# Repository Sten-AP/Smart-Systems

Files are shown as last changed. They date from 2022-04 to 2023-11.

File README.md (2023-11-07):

# Smart Systems

Sten Hulsbergen<br/>
2ITIOT<br/>

# Portfolio

## Korte beschrijving van het project

Het project is het ontwerpen van een smart car. De PCB's worden individueel gemaakt en de auto moet automatisch alsook manueel bestuurbaar kunnen zijn met embedded software.

### Wat is het doel van het project?

Het doel is om een analyse te maken en met deze analyse het project op te bouwen. Dit houdt in dat er PCB's ontworpen moesten worden, gemaakt en bestukt. Later dan software ontwikkelen en de wagen testen.

### Wat is er gerealiseerd?

- Analyse gemaakt
- PCB’s ontwropen
- PCB’s gefreesd
- PCB’s bestukt
- Software geschreven
- Wagen getest

## Toelichten van het finale ontwerp van het project:
### Wat waren de vereisten van het project?

De auto moest twee UART connectoren bevatten, drie I2C connectoren, de regelaar 7805 vervangen door een LDL1117 van 3.3V en 5V, polariteitsbeveiliging voorzien, motordriver aanpassen naar een SMD-type en een OLED-scherm met I2C sturing. Naast de sturing moesten een aantal sensoren voorzien worden, een linetracker, IR- en ultrasone afstandssensoren. Ook zullen er verkeerssignalisaties ontwikkeld moeten worden zoals verkeerslichten, slagbomen,... Als laatste moet de wagen manueel alsook automatisch bestuurd kunnen worden en een patroon kunnen rijden.

### Effectieve ontwerpen:
#### PCB Design
##### Sturingschakeling

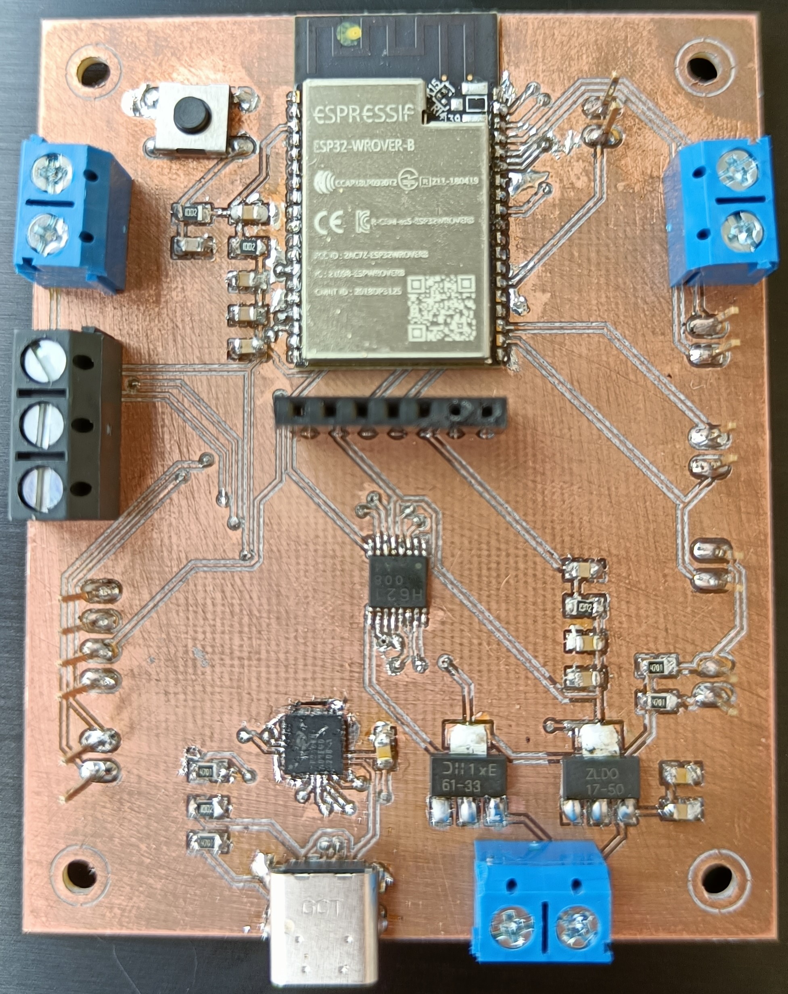
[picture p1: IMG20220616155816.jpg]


##### Sensorschakeling

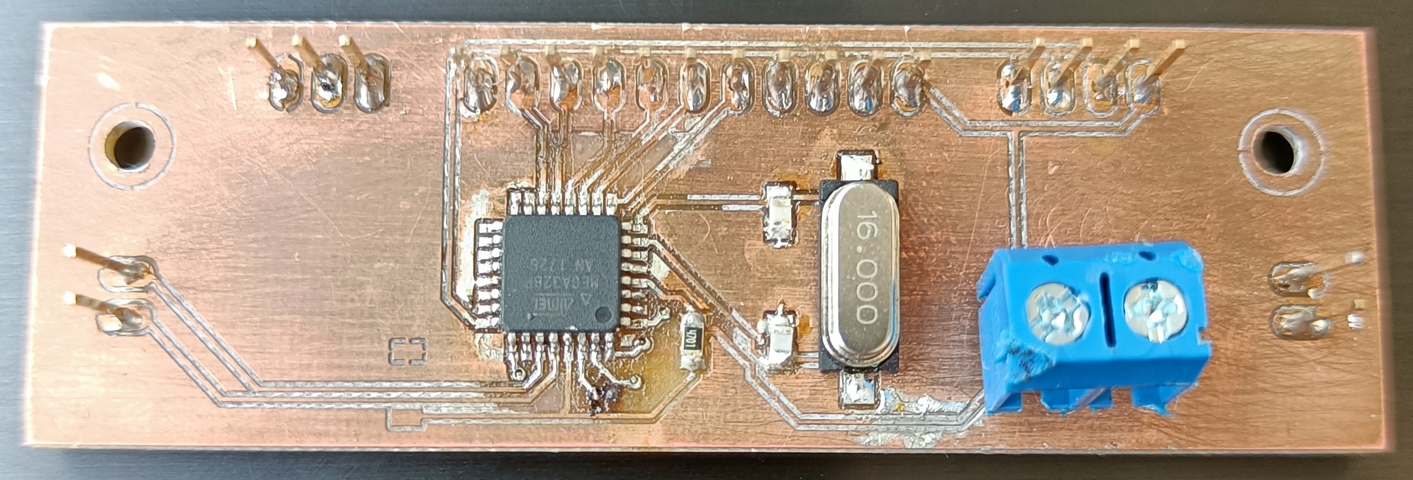
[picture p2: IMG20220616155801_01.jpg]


### Extra documentatie van de software 
De software is grotendeel opgebouwd uit enum's en switches. Dit maakt het makkelijk om duidelijke code te schrijven zonder dat deze moeilijk te lezen is door een andere persoon. De ESP32 maakt verbinding met het internet en dan de MQTT broker. Vervolgens initialiseerd de software allerlei nodige onderdelen zoals de serial monitor, etc in de setup. In de loop wordt steeds gekeken of de keuze in het menu op automatisch staat of op manueel. Als deze op automatisch staat, dan gebruikt de auto de linetracker en stuurd hij bepaalde commando's zoals links, rechts, voorwaards, etc. Als er gekozen was voor manueel, dan worden de waardes gebruikt die van de Node-RED besturing komen. Dit zijn knoppen om de gewenste richting ingeven. Om te wissel van modus kan dat via het dropdownmenu.

### Node-RED besturing
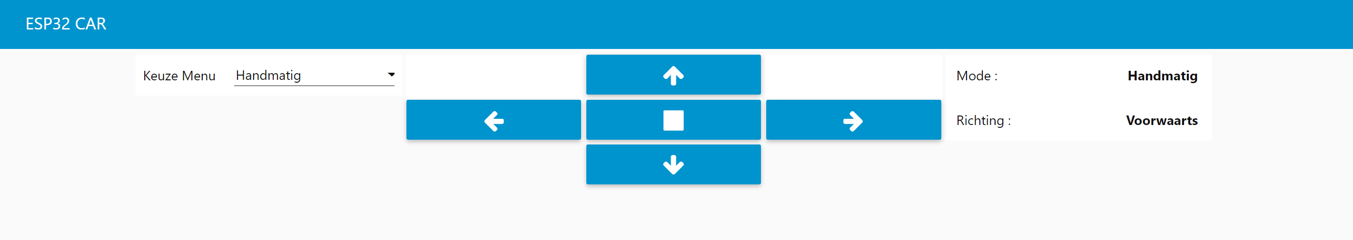
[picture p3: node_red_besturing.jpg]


### Node-RED
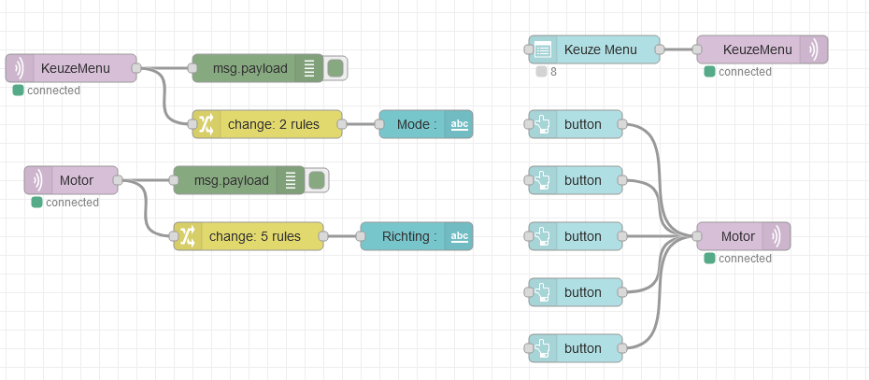
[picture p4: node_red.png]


### Flowchart


### Flowchart manuele besturing


### Testen en resultaten 

De tests zijn niet gedaan met de eigen ontworpen PCB's maar met de oude. Dit was nodig om de software toch een kans te kunnen geven om daar aan te kunnen werken. Deze software bevat een Node-RED en hiermee kan de auto succesvol automatisch rijden en manueel bestuurd worden. Er mist een deel van de software omdat de rest van de sensoren niet getest konden worden omdat er ook te weinig tijd was. Hiervan is een demo gemaakt om te laten zien tijdens de presentatie.

### Conclusie

Ik heb geleerd dat een analyse zeer belangrijk is in een project aangezien dit de basis is voor een project. Door op een goede manier alle componenten op te zoeken en de gegevens er van over te nemen, kan veel tijd bespaard worden later. In het begin moesten we allemaal apart werken aan ons project, later is gebleken dat dat niet echt kon en hielp iedereen elkaar. Het ontwerpen van de PCB's was niet makkelijk, zeker ook omdat het voelde alsof het uit het niks kwam vanwege een slechte uitleg. Door materiaaltekort en tijdsgebrek (lector een maand afwezig) is het project niet helemaal afgeraakt. Ik heb geprobeerd om de ontworpen PCB's zo goed mogelijk te ontwerpen al waren er een aantal onderdelen zo goed als niet te doen zoals de USB-C connector. De software is niet ontworpen voor deze schakelingen maar werkt wel op de oude PCB. Op deze manier is er toch nog een rijdende auto voorzien.

### Wat ik heb geleerd

- Fusion360
- PCB frezen
- Werken met de reflow oven
- Solderen
- Werken met ESP32
- Node-RED

### Verbeteringen 

Het aantal vias kan verminderd worden. De headers kunnen alleen langs de onderkant gesoldeerd worden dus de paden langs onder laten lopen.

Code ontbreekt voor de IR- en ultrasone sensor, alleen de ESP32 wordt gebruikt.

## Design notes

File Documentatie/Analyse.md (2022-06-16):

# Analyse
Sten Hulsbergen<br/>
2ITIOT<br/>

## Probleemstelling

Het grootste probleem wat er is, is dat er een volledig nieuwe wagen ontworpen moet worden. 
Deze moet twee UART connectoren bevatten, drie I2C connectoren, de regelaar 7805 vervangen door een LDL1117 van 3.3V en 5V, polariteitsbeveiliging voorzien, motordriver aanpassen naar een SMD-type en een OLED-scherm met I2C sturing. Naast de sturing moeten een aantal sensoren voorzien worden, een linetracker, IR- en ultrasone afstandssensoren. Ook zullen er verkeerssignalisaties ontwikkeld moeten worden zoals verkeerslichten, slagbomen,... Als laatste moet de wagen manueel alsook automatisch bestuurd kunnen worden en een patroon kunnen rijden.

## Mindmap



## Hardware analyse
### Hardware blokdiagram



### Specificatie tabel
| Blok | Specificatie | Min | Nominaal | Max |
|:---:|:---:|:-----:|:---:|:---:|
| Batterij | Spanning |  | 7.4V |  |
|  | Stroom | 700mA |  | 2A |
|  | Capaciteit |  | 1200mAh |  |
| TC78H621FNG | Spanning | 2.5V | 5V | 15V |
|  | Stroom |  | 0.8A | 1.1A |
| LDL1117S50R | Spanning |  | 5V |  |
|  | Stroom |  | 2A |  |
| LDL1117S33R | Spanning |  | 3.3V |  |
|  | Stroom | 500mA |  |  |
| ESP32 Wrover | Spanning | 2.7V | 3.3V | 3.6V |
|  | Stroom |  |  | 200mA |
| Atmega328p | Spanning | 1.8V | 5V | 5.5V |
|  | Stroom |  |  | 200mA |
| MJKDZ MIR-3.0Y | Spanning | 3V |  | 5V |
|  | Bereik |  | 40mm |  |
| GP2Y0A21YK0F | Spanning | 4.5V | 5V | 5.5V |
|  | Stroom |  | 30mA |  |
| HC-SR04 | Spanning |  | 5 V |  |
|  | Stroom | 2mA |  | 15mA |
| SSD1306 | Spanning | 3.3V |  | 5V |
| CP2102N-A02-GQFN28R | Spanning | 3V | 3.3V | 3.6V |
| USB4085-GF-A | Spanning |  | 5V |  |
|  | Stroom |  | 3A |  |

### Argumentatie en alternatieven tabel

| Blok | Argumentatie | Alternatieven |
|:---:|:---:|:-----:|
| ESP32 Wrover | De Wrover wordt rechtstreeks geplaatst op de PCB, dit maakt de gehele PCB goedkoper aangezien de ESP32 zelf ontworpen word met alleen alle benodigheden van de schakeling. |  |
| MJKDZ MIR-3.0Y | Om de wagen steeds recht te kunnen laten rijden en de baan zelfstandig te laten volgen, moeten we steeds kunnen weten waar de weg zich bevind. |  |
| GP2Y0A21YK0F | Deze IR-sensor is beschikbaar in grote hoeveelheden op school en is vrij makkelijk om mee te werken. Dient om de afstand naar een bepaald object te meten op kortere afstanden. | GP2Y0A41SK0F |
| HC-SR04 | Deze ultrasone sensor is beschikbaar in grote hoeveelheden op school en is vrij makkelijk om mee te werken. Dient om de afstand naar een bepaald object te meten op langere afstanden. |  |
| TC78H621FNG | Deze motor driver is gekozen omdat het SMD component is. De driver heeft twee inputs en outputs, dit maakt het makkelijker om te ontwerpen aangezien het een enkele component is en geen twee. | Twee motor drivers LA6583MC-AH |

## Software analyse
### Data in- en outputs
| Blok | Data in | Data out |
|:----:|:---:|:---:|
| IR-sensor | Digitaal IR aanzetten | Analoge spanningswaarde van ontvanger |
| Linetracker | Digitaal IR aanzetten | Analoge spanningswaarde van elke ontvanger |
| Ultrasoonsensor | Digitaal puls versturen | Digitaal puls ontvangen |
| OLED | I2C | n.v.t. |
| Motor driver | Analoog PWM signaal | Versterkt PWM signaal |
### State diagram
#### Manueel


#### Automatisch


#### Parkoer


### Flowchart


#### Flowchart manueel


## Release plan
### Epics
1. Analyse
2. PCB's ontwerpen
3. Software ontwikkelen
4. Hardware opbouwen
5. Software implementeren
6. Geheel testen

### Stories
#### 1. Analyse
* Probleemstelling
* Mindmap
* Hardware analyse
	* Hardware blokdiaram
	* Specificatie tabel
	* Argumentatie en alternatieven tabel
	* Elektrisch schema
		* Sturingsschakeling
		* Sensorschakeling
	* PCB ontwerp
		* Sturingsschakeling
		* Sensorschakeling
* Software analyse
	* Data in- en outputs
	* State diagram
		* Manueel
		* Automatisch
	* Flowchart
* Release plan

#### 2. PCB's ontwerpen
* Sturingsschakeling
	* ESP32 Wrover
	* 2x UART
	* 3x I2C
	* 5V en 3.3V spanningsregelaars
	* Polariteitsbeveiliging
	* SMD Motor driver
	* OLED met I2C
	* Batterij aansluiting
	* Montagegaten
* Sensor schakeling
	* Atmega328P
	* Ultrasone sensor
	* IR-sensor
	* Linetracker
	* Montagegaten

#### 3. Software ontwikkelen
* Manueel besturen
* Automatisch rijden
* Patroon volgen

#### 4. Hardware opbouwen
* Sturingsschakeling solderen
* Sensorschakeling solderen
* Robotwagen opbouwen

#### 5. Software implementeren
* ESP32 Wrover programmeren
* Atmega328p programmeren

#### 6. Geheel testen
* Componenten
* Data in & out
* Modussen

### Sprints
* Analyse
* PCB's ontwerpen
* Internationaal week Brugge
* Software ontwikkelen en hardware opbouwen
* Software implementeren & Geheel testen

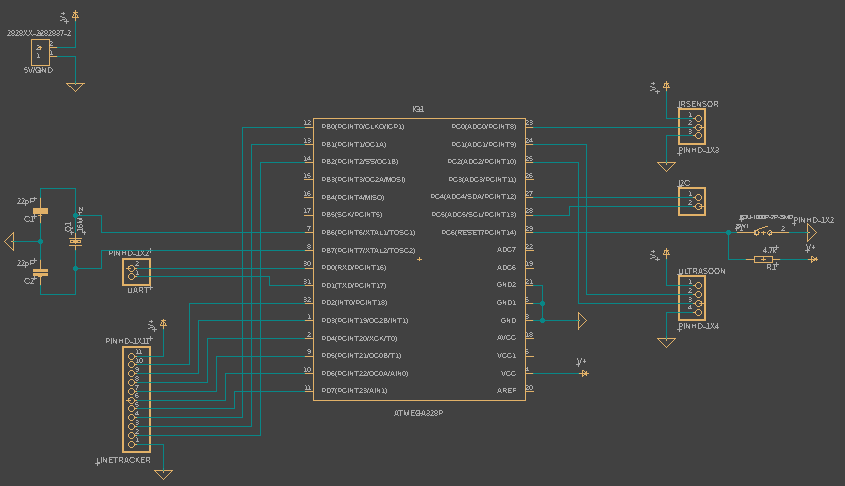
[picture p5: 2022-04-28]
Documentatie/Foto's en etc/SensorschakelingSCHEMA.png

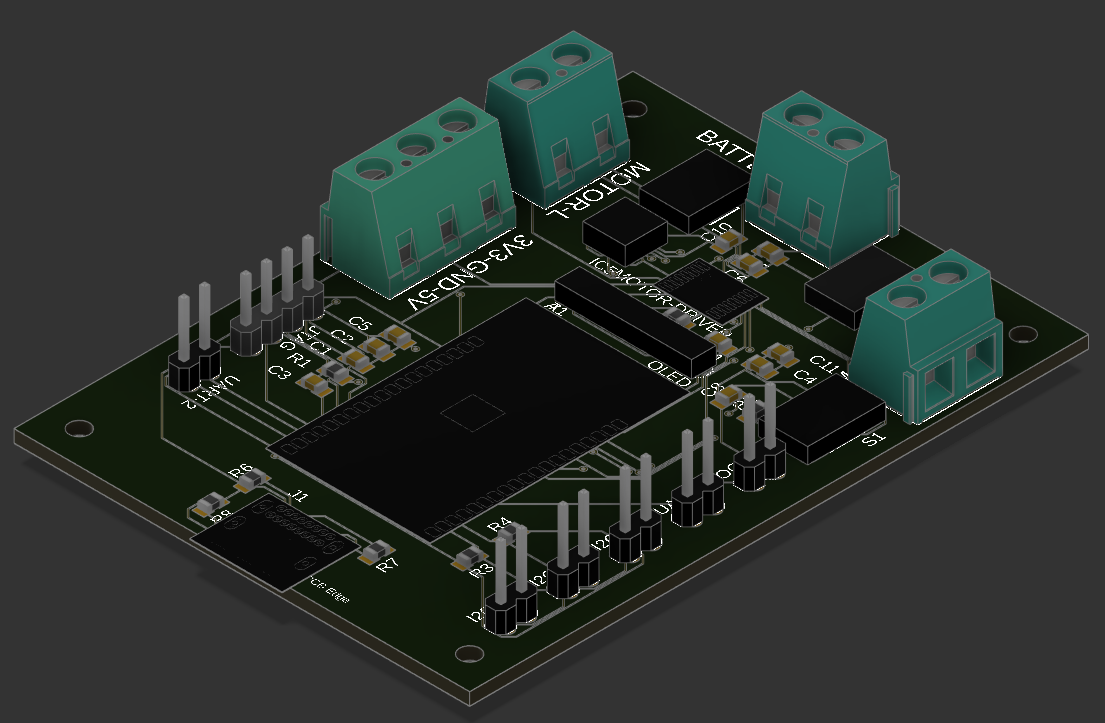
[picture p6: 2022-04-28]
Documentatie/Foto's en etc/SturingsschakelingPCB.png

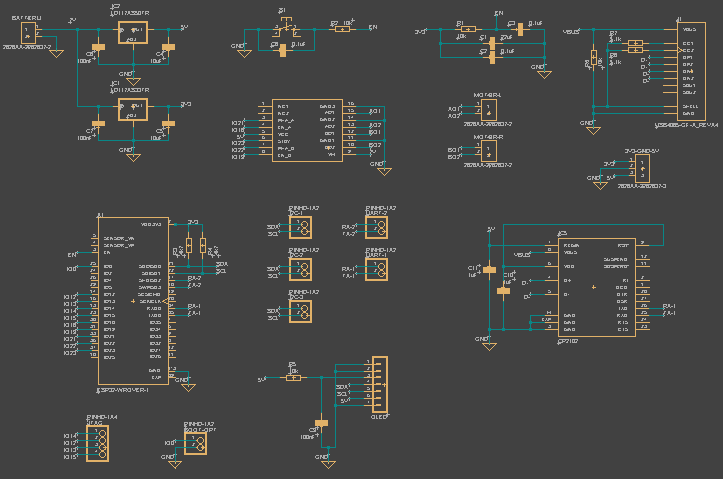
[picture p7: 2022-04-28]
Documentatie/Foto's en etc/SturingsschakelingSCHEMA.png

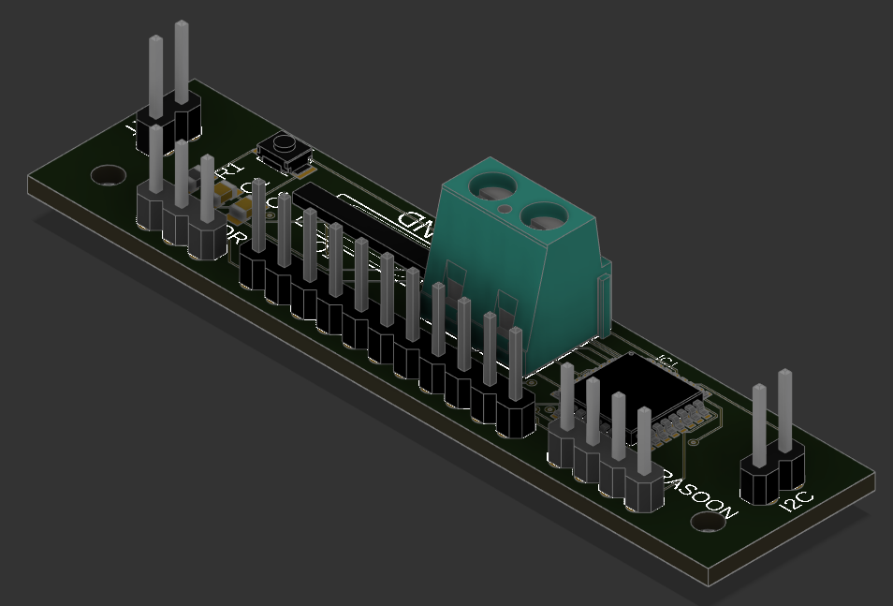
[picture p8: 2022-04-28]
Documentatie/Foto's en etc/SensorschakelingPCB.png

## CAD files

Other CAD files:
Docs/PCB/Sensorschakeling/PCB v21.f3d
PCB/Sensorschakeling/Electronics Design v61.f3z
PCB/Sensorschakeling/PCB v22.f3d

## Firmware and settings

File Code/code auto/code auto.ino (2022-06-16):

#include <LiquidCrystal_I2C.h> // https://github.com/johnrickman/LiquidCrystal_I2C (install as zip)
#include <WiFi.h>              // Standard ESP32 Library
#include <PubSubClient.h>      // https://github.com/knolleary/pubsubclient (intall with library Manager)

#define sub1 "Motor"
#define sub2 "KeuzeMenu"

const char* ssid = "brian";
const char* password = "12345678";
const char* mqtt_server = "mqtt.luytsm.be"; 

const char* username = "";
const char* pass = "";

WiFiClient espClient;
PubSubClient client(espClient);
unsigned long lastMsg = 0;
#define MSG_BUFFER_SIZE  (50)
char msg[MSG_BUFFER_SIZE];
int value = 0;

// PWM Settings - DO NOT CHANGE
const int PWM_FREQUENCY = 500;
const int PWM_RESOLUTION = 8;
const  int PWM_MAX_DC = 255;

// Motor PWM Pin declarations - DO NOT CHANGE
const int PWM_CHANNEL_COUNT = 4;
const int MOTOR_COUNT = 2;

int MOTOR_PINS[PWM_CHANNEL_COUNT] = {18, 5, 2, 15}; // Motor 1: 18, 5 -- Motor 2: 2, 15
int MOTOR_CHANNELS[PWM_CHANNEL_COUNT] = {0, 1, 2, 3};

// LED PWM Pin declarations - DO NOT CHANGE
const int LED_CHANNEL_COUNT = 4;
const int LED_COUNT = 4;

int LED_PINS[LED_COUNT] = {13, 12, 14, 27};
int LED_CHANNELS[LED_CHANNEL_COUNT] = {4, 5, 6, 7};
int LED_STATE[] = {0, 0, 0, 0};

// Linetracker
const int linetrackerLed[3] = {A4, A7, A6};

// Phototransitor Pin Declaration - DO NOT CHANGE 
const int PL_PIN = 25;
const int TRIG_PIN = 19;
const int ECHO_PIN = 23;

// I2C LCD Initialisation 
int LCD_COLUMNS = 16;
int LCD_ROWS = 2;
LiquidCrystal_I2C lcd(0x27, LCD_COLUMNS, LCD_ROWS);

char keuzeMenu;
char keuzeHandmatig;
int drivingSpeed = 200; // default 128

void setup_wifi()
{
  delay(10);
  // We start by connecting to a WiFi network
  Serial.println();
  Serial.print("Connecting to ");
  Serial.println(ssid);
  
  WiFi.begin(ssid, password);

  while (WiFi.status() != WL_CONNECTED) {
    delay(500);
    Serial.print(".");
  }

  randomSeed(micros());

  Serial.println("");
  Serial.println("WiFi connected");
  Serial.println("IP address: ");
  Serial.println(WiFi.localIP());
}

void callback(char* topic, byte* payload, unsigned int length)
{
  Serial.print("Message arrived [");
  Serial.print(topic);
  Serial.print("] ");
  Serial.println();
  if (strstr(topic, sub1))
  {
    for (int i = 0; i < length; i++)
    {
      Serial.println(char(payload[i]));
      keuzeHandmatig = char(payload[i]);
    }
  }
  else if (strstr(topic, sub2))
  {
    for (int i = 0; i < length; i++)
    {
      Serial.println(char(payload[i]));
      keuzeMenu = char(payload[i]);
    }
  }
  else
  {
    Serial.println("unsubscribed topic");
  }
}

void reconnect()
{
  // Loop until we're reconnected
  while (!client.connected()) {
    Serial.print("Attempting MQTT connection...");
    // Create a random client ID
    String clientId = "ESP8266Client-";
    clientId += String(random(0xffff), HEX);
    // Attempt to connect
    if (client.connect(clientId.c_str() , username, pass)) {
      Serial.println();
      Serial.println("connected");
      // Once connected, publish an announcement...
      client.publish("outTopic", "hello world");
      // ... and resubscribe
      client.subscribe(sub1);
      client.subscribe(sub2);
    } else {
      Serial.print("failed, rc=");
      Serial.print(client.state());
      Serial.println(" try again in 5 seconds");
      // Wait 5 seconds before retrying
      delay(5000);
    }
  }
}

enum COMMANDS {
  LEFT_TURN_FORWARD,      // 0
  FORWARD,                // 1
  RIGHT_TURN_FORWARD,     // ... 
  RIGHT,
  RIGHT_TURN_BACKWARDS,
  BACKWARDS,
  LEFT_TURN_BACKWARDS,
  LEFT,
  STOP,
  BARRIER_ONE_UP,
  BARRIER_ONE_DOWN,
  PRIOR_VEHICLE,
  BARRIER_TWO_UP,
  BARRIER_TWO_DOWN,     //13
};

enum MOTOR_DIRECTION {
  MOTOR_BACKWARDS = -1,
  MOTOR_STOP = 0,
  MOTOR_FORWARD = 1
};

enum MENUKEUZE {
  AUTOMATISCH = '8',
  HANDMATIG = '9'
};

enum HANDMATIG {
  LINKS = '0',
  RECHTDOOR = '1',
  RECHTS = '2',
  ACHTERUIT = '3'
};

int command, lastCommand;
int ledLinks, ledMidden, ledRechts;

void setup() {
  Serial.begin(115200);
  // init of the linetrackerLeds
  for (int i = 0; i < sizeof(linetrackerLed); i++) {
    pinMode(linetrackerLed[i], INPUT);
  }
  // init of the PWM Pins 
  for (int i = 0; i < PWM_CHANNEL_COUNT; i++) {
    ledcSetup(MOTOR_CHANNELS[i], PWM_FREQUENCY, PWM_RESOLUTION);
    ledcAttachPin(MOTOR_PINS[i], MOTOR_CHANNELS[i]);
  }
  //init of the LED Pins 
  for (int i = 0; i < LED_COUNT; i++) {
    ledcSetup(LED_CHANNELS[i], PWM_FREQUENCY, PWM_RESOLUTION);
    ledcAttachPin(LED_PINS[i], LED_CHANNELS[i]);
    ledcWrite(LED_CHANNELS[i], 128);
  }
  // init ultrasonic distance sensor
  pinMode(TRIG_PIN, OUTPUT); 
  pinMode(ECHO_PIN, INPUT); 

  // lcd init 
  lcd.init();
  lcd.backlight();

  setup_wifi();

  client.setServer(mqtt_server, 1883);
  client.setCallback(callback);
}

void loop() {
  if (!client.connected()) {
    reconnect();
  }
  client.loop();

  switch (keuzeMenu) {
    // Automatisch rijden van de wagen
    Serial.println(keuzeMenu);
    case AUTOMATISCH:
      ledLinks = analogRead(linetrackerLed[0]);
      ledMidden = analogRead(linetrackerLed[1]);
      ledRechts = analogRead(linetrackerLed[2]);

      Serial.println(String(ledLinks) + " - " + String(ledMidden) + " - " + String(ledRechts));

      if (ledLinks == 4095 && ledMidden == 4095 && ledRechts == 4095) command = LEFT;
      else if (ledMidden == 4095) command = FORWARD;
      else if (ledLinks == 4095) command = RIGHT;
      else if (ledRechts == 4095) command = LEFT;
      else if (ledMidden == 4095 && ledRechts == 4095) command = RIGHT;
      else if (ledMidden == 4095 && ledLinks == 4095) command = LEFT;
      break;
    // Handmatig besturen van de wagen
    case HANDMATIG:
      switch (keuzeHandmatig) {
        case LINKS:
          command = LEFT;
          break;
        case RECHTDOOR:
          command = FORWARD;
          break;
        case RECHTS:
          command = RIGHT;
          break;
        case ACHTERUIT:
          command = BACKWARDS;
          break;
        default:
          command = STOP;
          break;
      }
      break;
    default:
      break;
  }

  if (lastCommand != command) {
    switch (command) {
      case LEFT_TURN_FORWARD:  // Curved turn forward to the left
        driveMotors(MOTOR_FORWARD, drivingSpeed, MOTOR_FORWARD, drivingSpeed/4);
        break;
      case FORWARD: // Drive forward
        driveMotors(MOTOR_FORWARD, drivingSpeed, MOTOR_FORWARD, drivingSpeed);
        break;
      case RIGHT_TURN_FORWARD: // Curved turn forward to the right
        driveMotors(MOTOR_FORWARD, drivingSpeed/4, MOTOR_FORWARD, drivingSpeed);
        delay(2000);
        break;
      case RIGHT: // Turn right around center point chassis
        driveMotors(MOTOR_BACKWARDS, drivingSpeed/4, MOTOR_FORWARD, drivingSpeed/4);
        break;
      case RIGHT_TURN_BACKWARDS: // Curved turn backwards to the right
        driveMotors(MOTOR_BACKWARDS, drivingSpeed/2, MOTOR_BACKWARDS, drivingSpeed);
        break;
      case BACKWARDS: // Drive backwards
        driveMotors(MOTOR_BACKWARDS, drivingSpeed, MOTOR_BACKWARDS, drivingSpeed);
        break;
      case LEFT_TURN_BACKWARDS: // Curved turn backwards to the right 
        driveMotors(MOTOR_BACKWARDS, drivingSpeed, MOTOR_BACKWARDS, drivingSpeed/2);
        break;
      case LEFT: // Turn left around center point chassis
        driveMotors(MOTOR_FORWARD, drivingSpeed/4, MOTOR_BACKWARDS, drivingSpeed/4);
        break;
      case STOP: // Stop driving
        driveMotors(MOTOR_STOP, 0, MOTOR_STOP, 0);
        break;
      case BARRIER_ONE_UP: //Raise barrier 1 up
        barrierControl(0, true);
        break;
      case BARRIER_ONE_DOWN: //Lower barrier 1 down
        barrierControl(0, false);
        break;
      case PRIOR_VEHICLE: //Start the priority vehicle protocol 
        priorVehicle();
        break;
      case BARRIER_TWO_UP: //Raise barrier 2 up
        barrierControl(1, true);
        break;
      case BARRIER_TWO_DOWN: //Lower barrier 2 down
        barrierControl(1, false);
        break;
      default: //Set the driving speed 
        drivingSpeed = command;
        break;
    }
  }
  lastCommand = command; //Another question on the assignment, why is this statement necessary 
}

void driveMotors(int leftMotorDirection, int leftMotorSpeed, int rightMotorDirection, int rightMotorSpeed) {
  switch (leftMotorDirection) {
    case MOTOR_FORWARD:
      ledcWrite(MOTOR_CHANNELS[1], leftMotorSpeed);
      ledcWrite(MOTOR_CHANNELS[0], 0);
      break;
    case MOTOR_BACKWARDS:
      ledcWrite(MOTOR_CHANNELS[1], 0);
      ledcWrite(MOTOR_CHANNELS[0], leftMotorSpeed);
      break;
    default:
      ledcWrite(MOTOR_CHANNELS[1], 0);
      ledcWrite(MOTOR_CHANNELS[0], 0);
      break;
  }

  switch (rightMotorDirection) {
    case MOTOR_FORWARD:
      ledcWrite(MOTOR_CHANNELS[2], rightMotorSpeed);
      ledcWrite(MOTOR_CHANNELS[3], 0);
      break;
    case MOTOR_BACKWARDS:
      ledcWrite(MOTOR_CHANNELS[2], 0);
      ledcWrite(MOTOR_CHANNELS[3], rightMotorSpeed);
      break;
    default:
      ledcWrite(MOTOR_CHANNELS[2], 0);
      ledcWrite(MOTOR_CHANNELS[3], 0);
      break;
  }
}

void barrierControl(int barrierID, bool setBarrier) {
  digitalWrite(barrierID, setBarrier);
}

void priorVehicle() {

}

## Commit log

2022-05-05 folder move
    [PCB v21.f3d]
2022-05-06 PCB aanpassing
